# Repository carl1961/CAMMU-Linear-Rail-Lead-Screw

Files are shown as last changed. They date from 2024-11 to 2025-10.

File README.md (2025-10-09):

# CAMMU with Linear Rail Lead Screw and front mounted customized CAMUU Gates

[CAMMU Facebook](https://www.facebook.com/groups/996841964765478)

CAMMU-Linear-Rail-Lead-Screw

First Thanks  to  camnefdt/CAMMU https://github.com/camnefdt/CAMMU   for his work and allowing us to have fun.

Step and Stl files in Linear Rail, feel free to improve.

Front Selector 250mm Linear rail MGN9 9mm MGN9C block
Top back Selector  300mm Linear MGN9 9mm MGN9C block
Lead Screw 270mm 

# Progress

Filamentalist_V3_CAMMU_Enclosue v19

[CAMMU-Linear-Rail-Lead-Screw Test](https://www.facebook.com/share/v/1BHCnjoqrM/)

Drill Bit Handles for hand drilling parts
Drill Bit Handle v2

Needed to add PC4-M6 fitting for the Filamentalist Spool winder to work.




WIN_20250928_00_52_30_Pro

WIN_20250930_00_51_32_Pro

New Gate needs Slide nuts with these 12mm dummy slider spacers to keep nuts within range to bolt gates.

WIN_20250929_01_24_08_Pro

Made some changes to the original Gate, added bearings on the henges and made mounting in front , makes it easer to remove if need to be repaired. made some other minor changes too.

WIN_20250929_23_52_04_Pro  WIN_20250930_00_02_21_Pro

WIN_20250930_00_03_26_Pro  



You must use slider nuts instead of the hamer head nuts, so you will be able to hook the top. This also gave mor support for when the selector presses down to clamp filament.

lead screw came off a old anycubic I3  P, 





# CAMMU - V1

CAMMU is a universal multi material filament system, inspired by ERCF and Tradrack systems but designed to use no servo at all and keep components as accessible as possible.

A full custome controller and DIY controller is currently in the works and to be released soon. 2 stepper ports and 6 endstop connections are all that is needed if you build the 4 gate version.

Please feel free to contribute towards future projects and developments

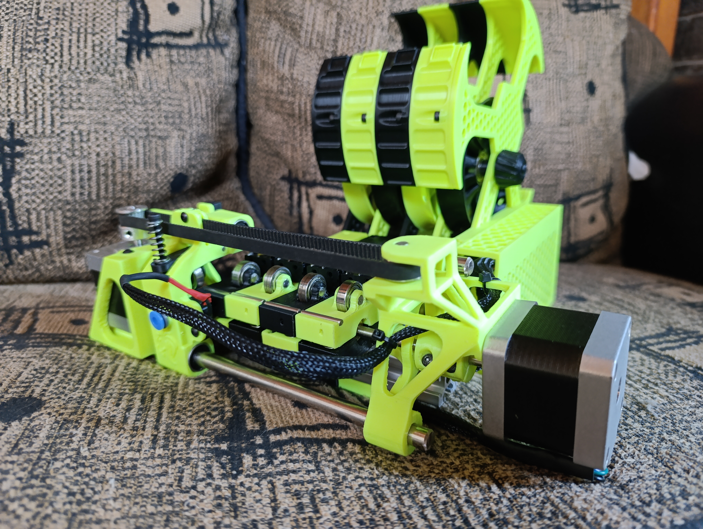
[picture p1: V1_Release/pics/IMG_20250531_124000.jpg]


[image]: https://github.com/camnefdt/CAMMU/blob/main/V1_Release/pics/IMG_20250531_124000.jpg
### Updates
- 06-08-2025:
    - Added CAMMU Gate Spacer to make the gate spacing a lot simpler
- 06-06-2025:
    - CAMMU Full release V1
    - Fixed folder structure and renamed old Beta to "CAMMU_Old"
    - Added modified ERCT-Cotton tail buffer files
    - **NOTE** The Cotton tail end cap with electronics was modified to fit BTT mmb V2 which is different size and mounting hole to MMB v1.
- 05-06-2025:
  - Added strengthened drive ends
  - Added slightly adjusted tension arm to align better on gate.
  - Added completed project photo.
- 01-04-2025:
  - Added modified top gate with thickened rear section for limit switch mount and enlarged screw holes for m3 screws.
- 12-03-2025:
  - Added build manual V1.
- 19-01-2025:
  - Added modified selector body to prevent premature wear of housing body.
  - Added slots to limit switch mounting on selector body.
  - Added strengthened selector drive end to limit unnecesary flex.
  - Moved extrude drive end idler pulley inward to make system more compact
  - Added more material on the bottom gate pivot ears to strengthen.
  - Modified to match new bottom gate ears as well as slotted limit switch mounting holes.
- 08-12-2024:
  - Added Build FAQ 
- 05-12-2024:
  - Add in basic instructions for assembly

### Build FAQ
- For the buffer, the ERCT (Cotton tail) buffer is a perfect fit. [***HERE***](https://github.com/Enraged-Rabbit-Community/ERCF_v2/tree/master/Recommended_Options/ERCT_Buffer)
- For the software control aspect of CAMMU, we decided to not reinvent the wheel and make use of the fantastic existing software called **Happy Hare** by moggieuk. You can find his github page [***HERE***](https://github.com/moggieuk)
  - You are requied to [***install Happy Hare***](https://github.com/moggieuk/Happy-Hare/wiki/Installation) on your existing klipper installation.
  - In due time we will compile a short guide on the installation and configuration of **Happy Hare**
- For the sensing aspect, not only do you require a filament sensor per gate, but also require a filament sensor on your toolhead
  - If you currently use the Sherpa range:
    - You can find a fantastic toolhead sensor for [***Sherpa Mini***](https://github.com/v6cl/MyDIYthings/tree/main/3Dprinters/AnnexEngineeringMOD/SherpaMini/SherpaMiniFilamentSensor).
      - This is a fantastic toolhead sensor and can easily be wired up to your existing toolhead board if you have one.
  - You also require a filament cutter on your toolhead as
    - The one we recommend and have tested can be found on Prusa Printables [***HERE***](https://www.printables.com/model/622289-filament-cutter-for-sherpa-and-sherpa-patterned-ex/files)

buy me a coffee
[***HERE***](https://www.buymeacoffee.com/camnefdt)


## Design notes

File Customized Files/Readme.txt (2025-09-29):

Gate bottom (NEW) takes 2 MR63zz bearings 3x6x2.5  , some list it as 3x6x3
Require to use 2020 M5 slide nuts
12mm Slider Nut dummy spacers, used to space Slider nuts the 22mm spacing

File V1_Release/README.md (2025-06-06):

V1 of CAMMU
Custom designed multi material system using no servo whatsoever

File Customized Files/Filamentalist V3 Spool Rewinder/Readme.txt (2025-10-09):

ALL still a work in progress!

My parts used in my 8 color Filamentalist Frame I did with 2020 extrusion
I resized clearance on parts at points to make easeir to assymble, for example the 8mm shaft I did 8.25mm  etc...  Filamentalist has everything exact measurements.

Also (optional) included or 3 drill handles I designed to make hand drilling, for the pockets for the earas to fit, I used M3 inserts for using 3mm allen screws to tighten the drill bit in handle.

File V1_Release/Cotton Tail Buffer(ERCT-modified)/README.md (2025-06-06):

Cotton tail buffer as found at: [***HERE***](https://github.com/Enraged-Rabbit-Community/ERCF_v2/tree/master/Recommended_Options/ERCT_Buffer)

Modified to suite CAMMU. 
This is the recommended option which fits perfect with CAMMU system

The electronic box was modified to fit BTT mmb V2 which is a different size and has different mounting holes copmpared to V1.

The bunny logo was also removed to make for easier printing.

The filament sensor space on filament blocks were removed as they are not necessary on CAMMU.

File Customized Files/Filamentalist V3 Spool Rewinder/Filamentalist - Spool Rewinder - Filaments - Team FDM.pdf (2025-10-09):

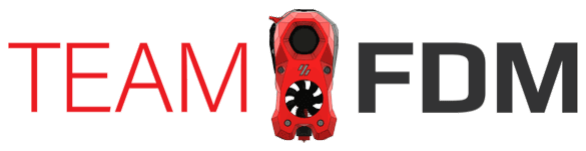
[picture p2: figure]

Filaments (https://www.teamfdm.com/forums/forum/38-filaments/)
- (https://www.teamfdm.com/discover/)
- (https://www.teamfdm.com/search/)

Home (https://www.teamfdm.com/) | Forums (https://www.teamfdm.com/forums/) | TeamFDM (https://www.teamfdm.com/forums/forum/17-teamfdm/) | Filaments (https://www.teamfdm.com/forums/forum/38-filaments/) | All Activity (https://www.teamfdm.com/discover/)

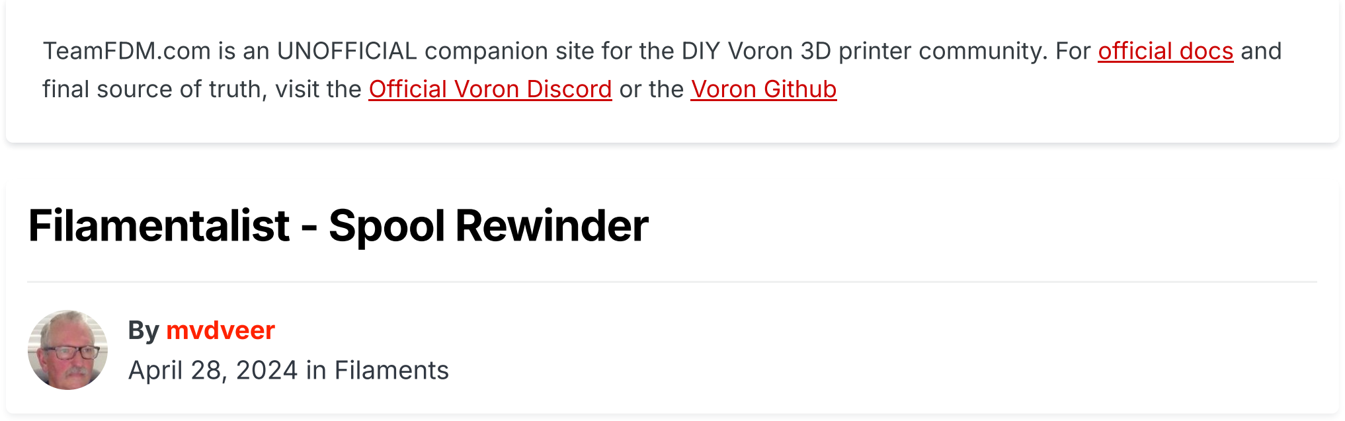
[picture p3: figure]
Filamentalist - Spool Rewinder; By mvdveer April 28, 2024 in Filaments

Reply to this topic

- (https://www.teamfdm.com/) | (https://www.teamfdm.com/forums/) | (https://www.teamfdm.com/forums/forum/17-teamfdm/) | (https://www.teamfdm.com/forums/forum/38-filaments/)

Filamentalist - Spool Rewinder
- (https://www.teamfdm.com/discover/)

TeamFDM.com is an UNOFFICIAL companion site for the DIY Voron 3D printer community. For official docs (https://bit.ly/VoronDocs) and final source of truth, visit the Official Voron Discord (https://bit.ly/VoronDiscord) or the Voron Github (https://bit.ly/VoronGitHub)

### mvdveer (https://www.teamfdm.com/profile/1268-mvdveer/)

Posted (https://www.teamfdm.com/forums/topic/3582-filamentalist-spool-rewinder/?do=findComment&comment=20390) April 28,
2024 (https://www.teamfdm.com/forums/topic/3582-filamentalist-spool-rewinder/?do=findComment&comment=20390)
- (https://www.teamfdm.com/profile/1268-mvdveer/)

Been looking for a good spool rewinder to use with the tradrack mounted on the Trident. Thanks to @PFarm (https://www.teamfdm.com/profile/5848-pfarm/) , I took a liking to the Filamentalist Spool Rewinder. (https://github.com/SkiBikePrint/ERCF_Mods/tree/main/Filamentalist) Tried quite a few and was not really happy with the solution I mounted on the Trident (Stern Wheeler Filament buffer). (https://www.printables.com/model/615902-stern-wheeler-filament-buffer-customizeable) Though it did not take up much space, it did not offer a flawless experience.

I also thought of the Universal Auto Rewind spool holder (https://www.printables.com/model/168-universal-auto-rewind-spool-holder-mm) by Vincent Groenhuis, as posted by @Buurman (https://www.teamfdm.com/profile/2667-buurman/) , but had an awful lot of trouble printing the springs to my satisfaction. Gave up on that one (heaps of parts in a tub, minus the springs).

So, filamentalsit seemed like a good idea, especially after watching the device in action:

https://www.youtube.com/watch?v=4iaSJrHc7k4

https://www.youtube.com/watch?v=W6pqgNZXvYI

Instructions on the GitHub page are comprehensive but I still found it confusing at times, and some steps that seemed obvious were omitted, like putting the rubber bands on the large pulleys.

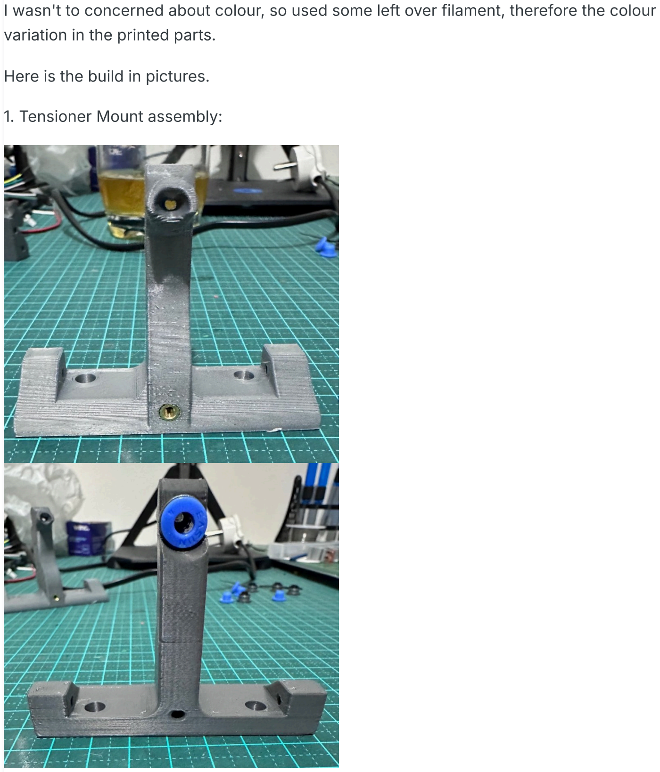
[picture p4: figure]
variation in the printed parts.; Here is the build in pictures.; 1. Tensioner Mount assembly:

I wasn't to concerned about colour, so used some left over filament, therefore the colour

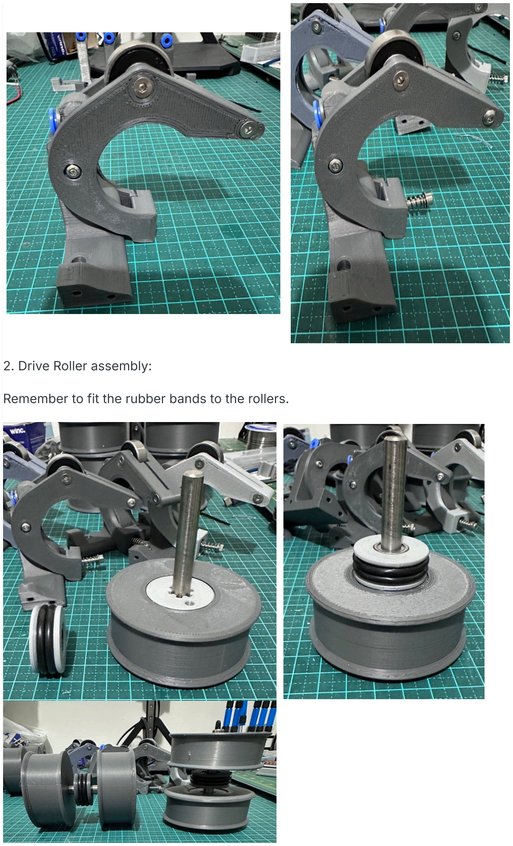
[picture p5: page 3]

2. Drive Roller assembly:

Remember to fit the rubber bands to the rollers.

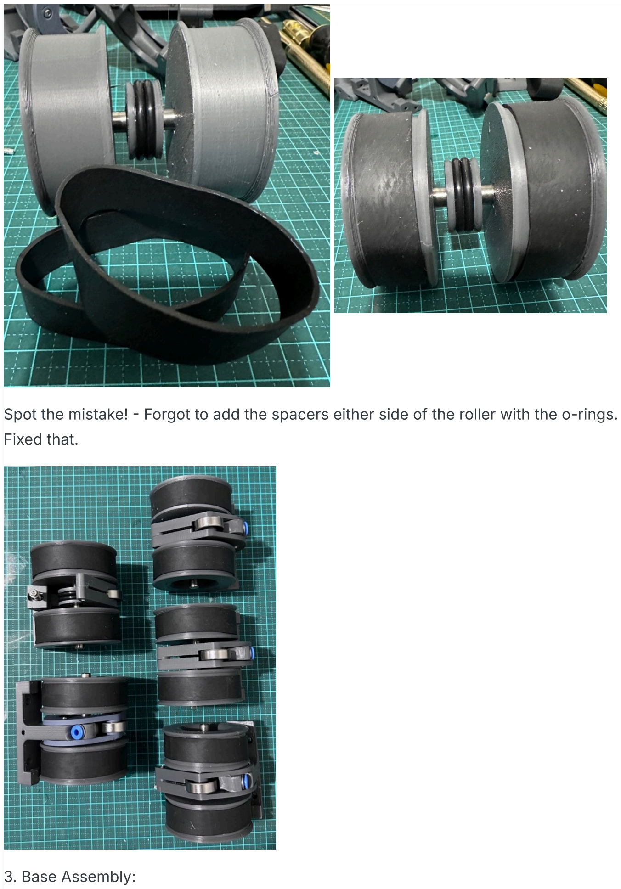
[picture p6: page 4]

Spot the mistake! - Forgot to add the spacers either side of the roller with the o-rings. Fixed that.

3. Base Assembly:

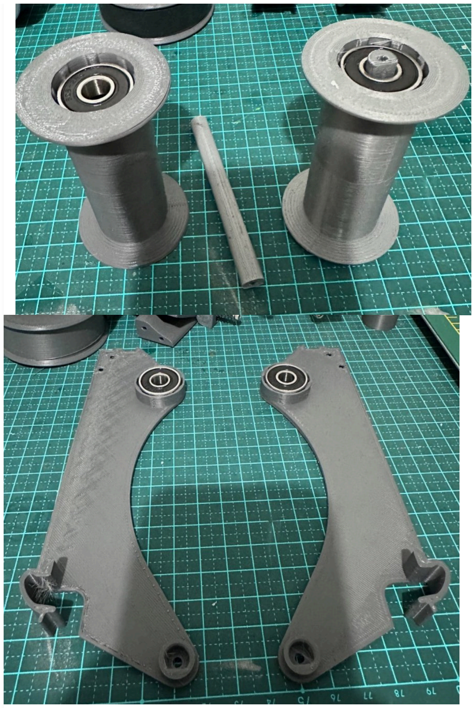
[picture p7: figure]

(Too much squish on the left pillar - see the wavey pattern)

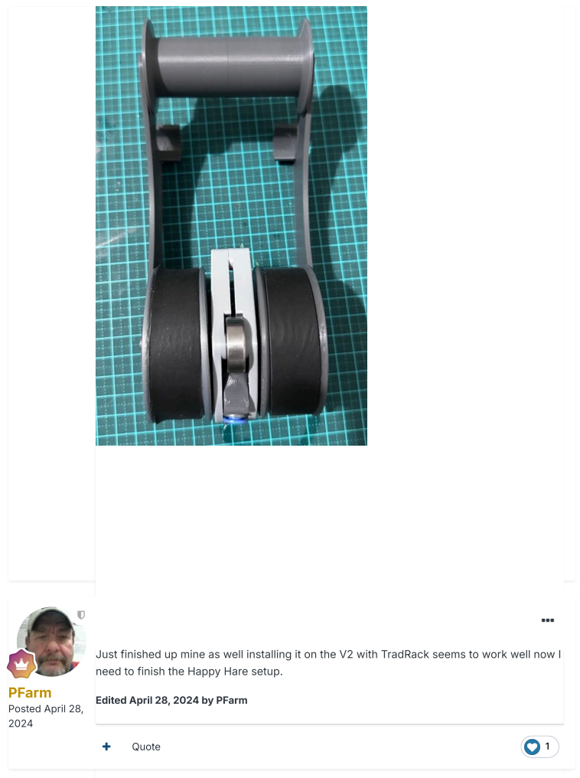
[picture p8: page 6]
PFarm; Posted April 28, 2024; Quote

Just finished up mine as well installing it on the V2 with TradRack seems to work well now I
need to finish the Happy Hare setup.

Edited April 28, 2024 by PFarm

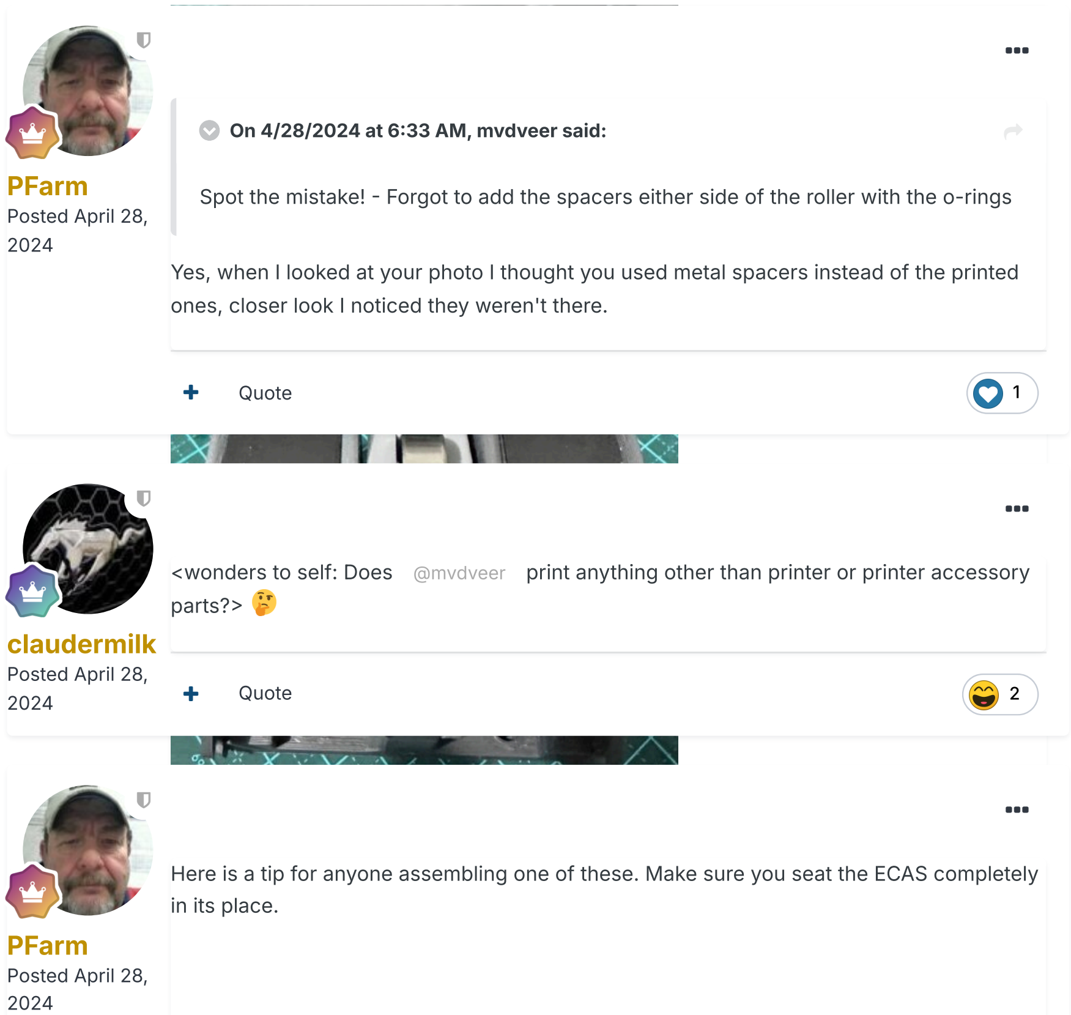
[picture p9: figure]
4. Finished Product:; PFarm; Posted April 28, 2024; Quote; On 4/28/2024 at 6:33 AM, mvdveer said:; claudermilk; parts?>; in its place.

Yes, when I looked at your photo I thought you used (https://www.teamfdm.com/uploads/monthly_2024_04/IMG_6572.jpeg.874148286c1fcb7fde601b39d7dd90a9.jpeg) metal spacers instead of the printed ones, closer look I noticed they weren't there.

Spot the mistake! - Forgot to add the spacers either (https://www.teamfdm.com/uploads/monthly_2024_04/IMG_6572.jpeg.874148286c1fcb7fde601b39d7dd90a9.jpeg) side of the roller with the o-rings

<wonders to self: Does @mvdveer print anything other (https://www.teamfdm.com/uploads/monthly_2024_04/IMG_6572.jpeg.874148286c1fcb7fde601b39d7dd90a9.jpeg) than printer or printer accessory

Here is a tip for anyone assembling one of these. Make sure you seat the ECAS completely

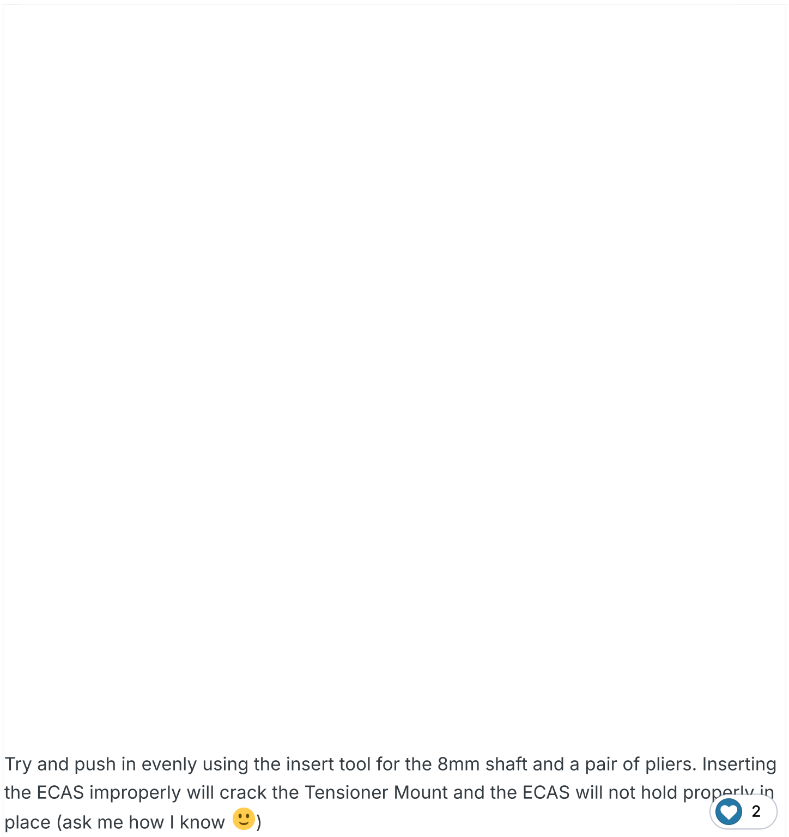
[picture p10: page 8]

And... it works! Even with these new cardboard spools - I do not like cardboard spools (https://www.teamfdm.com/uploads/monthly_2024_04/IMG_2212.JPG.8d0371010d1b7c2a49142156d88ff5b7.JPG) -just saying.

These will be installed on 2020 extrusion, mounted on top of the Trident. Thus, it will (https://www.teamfdm.com/uploads/monthly_2024_04/IMG_2212.JPG.8d0371010d1b7c2a49142156d88ff5b7.JPG) hide the tradrack at the back (https://www.teamfdm.com/uploads/monthly_2024_04/IMG_2212.JPG.8d0371010d1b7c2a49142156d88ff5b7.JPG)

Another enjoyable and easy build.

- Quote

Try and push in evenly using the insert tool for the 8mm shaft and a pair of pliers. Inserting the ECAS improperly will crack the Tensioner Mount and the ECAS will not hold properly in place (ask me how I know )

2

Got them installed on the 2020

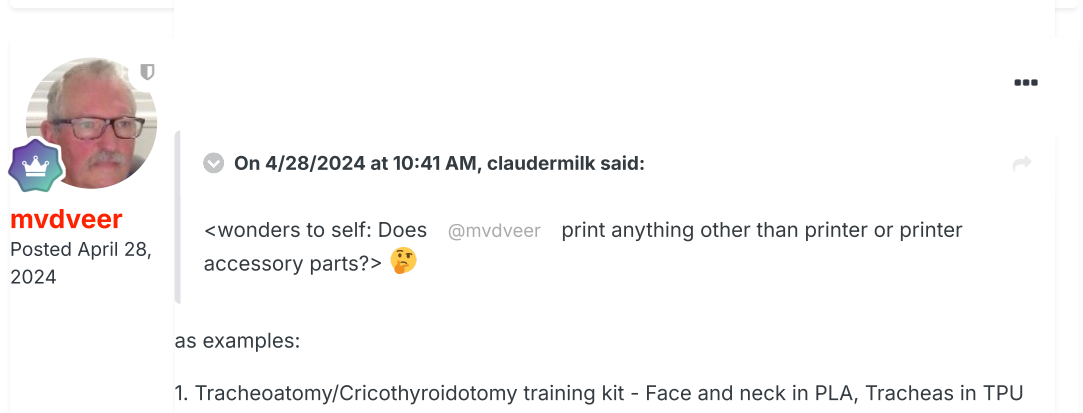
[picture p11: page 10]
mvdveer; Posted April 28, 2024; as examples:

On 4/28/2024 at 10:41 AM, claudermilk said:

<wonders to self: Does @mvdveer print anything other than printer or printer
accessory parts?>

1. Tracheoatomy/Cricothyroidotomy training kit - Face and neck in PLA, Tracheas in TPU

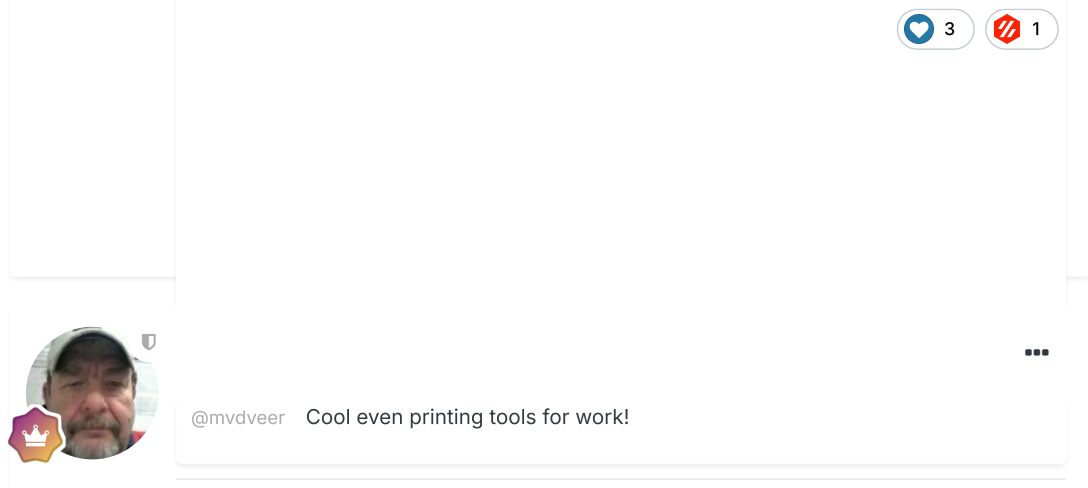
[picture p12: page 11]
Quote

Edited April 29, 2024 by PFarm

(https://www.teamfdm.com/profile/5848-pfarm/)

@mvdveer Cool even printing tools for work! (https://www.teamfdm.com/uploads/monthly_2024_04/IMG_5512.png.775a7b3a7bd59620c0779ff4b69a714a.png)

2. Marcus Aerilius Bust - PLA Marble - pre "post printing processing:
- Quote

### PFarm (https://www.teamfdm.com/profile/5848-pfarm/)

Posted (https://www.teamfdm.com/forums/topic/3582-filamentalist-spool-rewinder/?do=findComment&comment=20411) April 28,
2024 (https://www.teamfdm.com/forums/topic/3582-filamentalist-spool-rewinder/?do=findComment&comment=20411)
- Quote

### Graymattor (https://www.teamfdm.com/profile/10383-graymattor/)

Posted (https://www.teamfdm.com/forums/topic/3582-filamentalist-spool-rewinder/?do=findComment&comment=20423) April 29,
2024 (https://www.teamfdm.com/forums/topic/3582-filamentalist-spool-rewinder/?do=findComment&comment=20423)

# G (https://www.teamfdm.com/profile/10383-graymattor/)

Thanks for sharing your experiences,

I have been looking at the Filamentalis (https://www.teamfdm.com/uploads/monthly_2024_04/IMG_6302.png.69055e738b2675f11c40c1fc338679d3.png)t for a while now, due to space constraints (https://www.teamfdm.com/uploads/monthly_2024_04/IMG_6303.png.29f3bddd6825d8a3c81160afd4d6465b.png) a buffer was going to be difficult, and this woul (https://www.teamfdm.com/uploads/monthly_2024_04/IMG_6302.png.69055e738b2675f11c40c1fc338679d3.png)d be perfect for my 'future' set up! there (https://www.teamfdm.com/uploads/monthly_2024_04/IMG_6303.png.29f3bddd6825d8a3c81160afd4d6465b.png) appears to be quire a few people know who have (https://www.teamfdm.com/uploads/monthly_2024_04/IMG_6302.png.69055e738b2675f11c40c1fc338679d3.png) had some great success with it, i need (https://www.teamfdm.com/uploads/monthly_2024_04/IMG_6303.png.29f3bddd6825d8a3c81160afd4d6465b.png) to order some parts for a printer build so i will (https://www.teamfdm.com/uploads/monthly_2024_04/IMG_6302.png.69055e738b2675f11c40c1fc338679d3.png) order the Filamentalist parts also (shame (https://www.teamfdm.com/uploads/monthly_2024_04/IMG_6303.png.29f3bddd6825d8a3c81160afd4d6465b.png) no AliExpress links, being in the UK i cann (https://www.teamfdm.com/uploads/monthly_2024_04/IMG_6302.png.69055e738b2675f11c40c1fc338679d3.png)ot use the Amazon links, however a lot (https://www.teamfdm.com/uploads/monthly_2024_04/IMG_6303.png.29f3bddd6825d8a3c81160afd4d6465b.png) of items do come up on Amazon when copying the descriptions.

Please continue to share your experiences as you use it and of course set up with Happy Hare, which is something i am not looking forward to!!

Thanks

- Quote

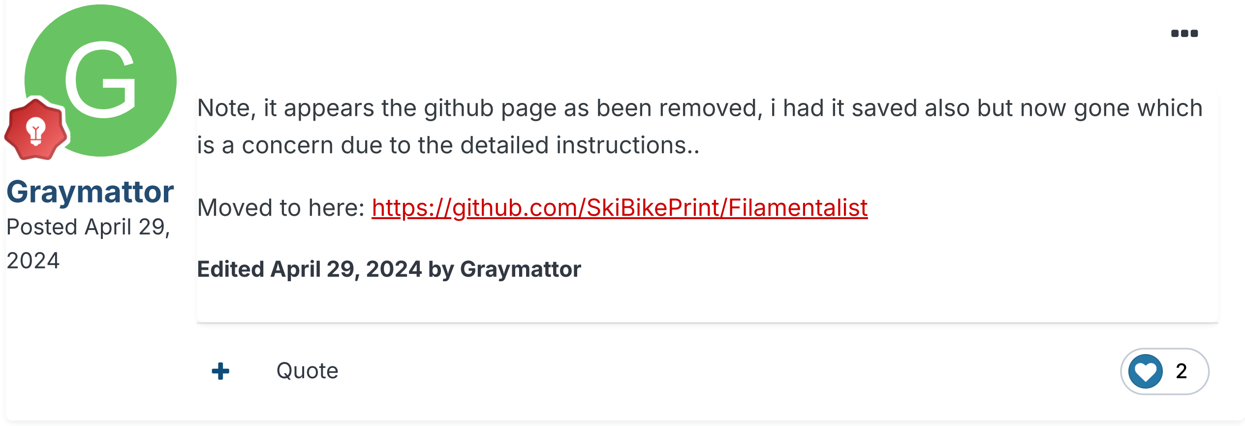
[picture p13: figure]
Graymattor; Posted April 29, 2024; Moved to here: https://github.com/SkiBikePrint/Filamentalist; Edited April 29, 2024 by Graymattor; Quote

Note, it appears the github page as been removed, i had it saved also but now gone which is a concern due to the detailed instructions..

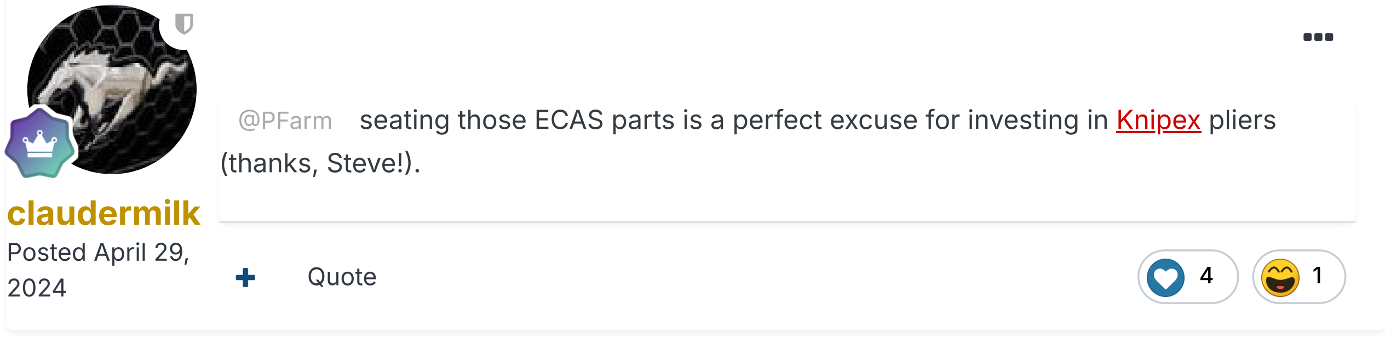
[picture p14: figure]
claudermilk; Posted April 29, 2024; (thanks, Steve!).; Quote

@PFarm (https://www.teamfdm.com/profile/5848-pfarm/) seating those ECAS parts is a perfect excuse for investing in Knipex (https://amzn.to/3IGSgyu) pliers

4

1

2

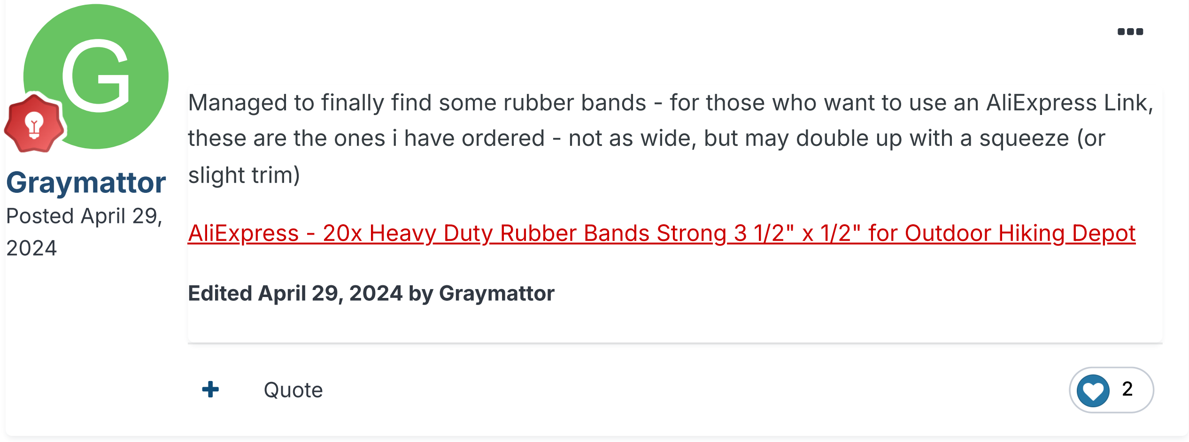
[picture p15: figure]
Graymattor; Posted April 29, 2024; slight trim); Edited April 29, 2024 by Graymattor; Quote

Managed to finally find some rubber bands - for those who want to use an AliExpress Link, these are the ones i have ordered - not as wide, but may double up with a squeeze (or

AliExpress - 20x Heavy Duty Rubber Bands Strong 3 1/2" x 1/2" for Outdoor Hiking Depot (https://www.aliexpress.com/item/1005006315999981.html?src=google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)

### PFarm (https://www.teamfdm.com/profile/5848-pfarm/)

Posted (https://www.teamfdm.com/forums/topic/3582-filamentalist-spool-rewinder/?do=findComment&comment=20439) April 29,
2024 (https://www.teamfdm.com/forums/topic/3582-filamentalist-spool-rewinder/?do=findComment&comment=20439)
- (https://www.teamfdm.com/profile/5848-pfarm/)

That should work mine were 3/4" wide as long as you push the rubber band toward the outside edge of the roller that's where the filament reel makes contact.

On 4/29/2024 at 9:51 AM, Graymattor (https://www.teamfdm.com/?app=core&module=members&controller=profile&id=10383) said:

Managed to finally find some rubber bands - for those who want to use an AliExpress Link, these are the ones i have ordered - not as wide, but may double up with a squeeze (or slight trim)

AliExpress - 20x Heavy Duty Rubber Bands Strong 3 1/2" x 1/2" for Outdoor Hiking Depot (https://www.aliexpress.com/item/1005006315999981.html?src=google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)

- (https://www.teamfdm.com/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)

- Quote

### Graymattor (https://www.teamfdm.com/profile/10383-graymattor/)

Posted (https://www.teamfdm.com/forums/topic/3582-filamentalist-spool-rewinder/?do=findComment&comment=20444) April 29,
2024 (https://www.teamfdm.com/forums/topic/3582-filamentalist-spool-rewinder/?do=findComment&comment=20444)

# G (https://www.teamfdm.com/profile/10383-graymattor/)

Thanks or the info, i just could not find 3/4" wide bands any where!

All the parts i don't already have in a stash somewhere have been ordered, next to go on a printing marathon! i will be looking at setting up 12 of these! i think may be in a row of 7 and then 5 in front staggered to allow the PTFE through from the rear ones..

I have absolutely no idea what im doing, but down the hole i goooooo!!

At least i now know i don't need to build up the ERCT

Edited April 30, 2024 by Graymattor (https://www.teamfdm.com/uploads/monthly_2024_04/IMG_6569_Fotor.jpg.2aeb5aa6f53a69e8d7b8f7f7add18166.jpg)

- Quote

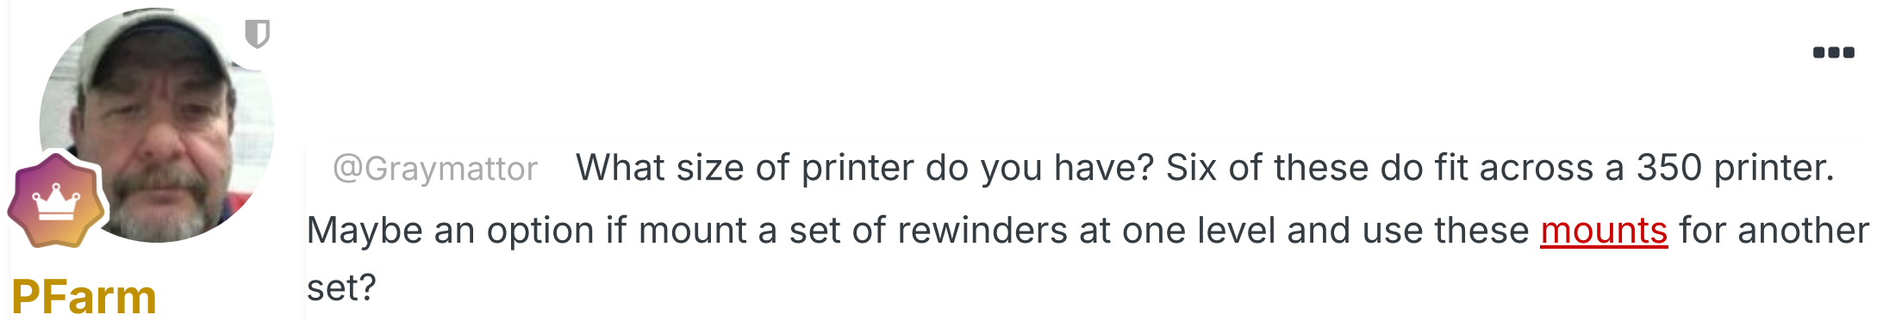
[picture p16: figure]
PFarm; set?

@Graymattor (https://www.teamfdm.com/profile/10383-graymattor/) What size of printer do you have? Six of these do fit across a 350 printer. Maybe an option if mount a set of rewinders at one level and use these mounts (https://www.printables.com/model/530709-offset-2020-mount-for-vorons) for another

21

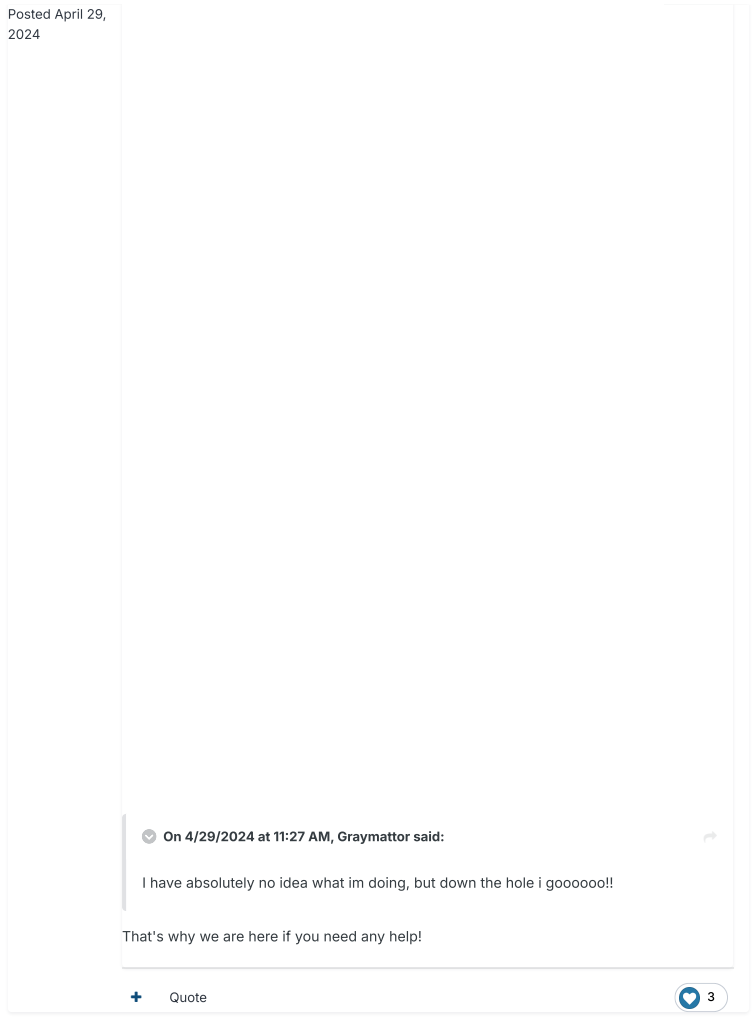
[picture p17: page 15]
Posted April 29, 2024; Quote

On 4/29/2024 at 11:27 AM, Graymattor (https://www.teamfdm.com/?app=core&module=members&controller=profile&id=10383) said:

I have absolutely no idea what im doing, but down the hole i goooooo!!

That's why we are here if you need any help!

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
### r (https://www.teamfdm.com/profile/10383-graymattor/)

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
ril 3

0

,
2

0

2

4 (https://www.teamfdm.com/forums/topic/3582-filamentalist-spool-rewinder/?do=findComment&comment=20480)

# G (https://www.teamfdm.com/profile/10383-graymattor/)

1 month later...

4 weeks later... (https://www.teamfdm.com/uploads/monthly_2024_04/e8276fa7-cbd9-46fb-b81e-03d47c97bf0e.jpg.f02f6d9da4d301cebe93664a2baefc46.jpg)

It's actually going in the top of a purpose built enclosure which is 600mm wide x 800mm deep... but need to fit 12 spools and the ERCF in there and allow enough room for the reverse bowden in to the printer compartment below...

Thank you.... When I start wiring, happy hare and integration that's when I'll hit a wall! I'll be using the MMB but currently I don't have a CAN printer (I have a klipperised CR-10

150 (https://www.teamfdm.com/profile/12812-wackocrash5150/) Posted (https://www.teamfdm.com/forums/topic/3582-filamentalist-spool-rewinder/?do=findComment&comment=22375) June 24, 2024 (https://www.teamfdm.com/forums/topic/3582-filamentalist-spool-rewinder/?do=findComment&comment=22375) | smart pro and I'm most of the way through building VZ330, i need to get both running CAN)..
- Quote

Wackocrash (https://www.teamfdm.com/profile/12812-wackocrash5150/)5 (https://www.teamfdm.com/uploads/monthly_2024_04/e8276fa7-cbd9-46fb-b81e-03d47c97bf0e.jpg.f02f6d9da4d301cebe93664a2baefc46.jpg)

Hello there. I just wanted to ask if you're still using (https://www.teamfdm.com/uploads/monthly_2024_04/e8276fa7-cbd9-46fb-b81e-03d47c97bf0e.jpg.f02f6d9da4d301cebe93664a2baefc46.jpg) these and if you're happy with them thus far? Any hiccups you've noticed? I too am looking (https://www.teamfdm.com/uploads/monthly_2024_04/e8276fa7-cbd9-46fb-b81e-03d47c97bf0e.jpg.f02f6d9da4d301cebe93664a2baefc46.jpg) to build a few of these for a Tradrack. Just ordered the BOM parts from Amazon. (https://www.teamfdm.com/uploads/monthly_2024_04/e8276fa7-cbd9-46fb-b81e-03d47c97bf0e.jpg.f02f6d9da4d301cebe93664a2baefc46.jpg) Thanks in advance.

- Quote (https://www.teamfdm.com/uploads/monthly_2024_04/e8276fa7-cbd9-46fb-b81e-03d47c97bf0e.jpg.f02f6d9da4d301cebe93664a2baefc46.jpg)

### mvdveer (https://www.teamfdm.com/profile/1268-mvdveer/)

Posted (https://www.teamfdm.com/forums/topic/3582-filamentalist-spool-rewinder/?do=findComment&comment=22379) June 24,
2024 (https://www.teamfdm.com/forums/topic/3582-filamentalist-spool-rewinder/?do=findComment&comment=22379)
- (https://www.teamfdm.com/profile/1268-mvdveer/)

Yes - they have been working without an issue

- Quote

On 6/24/2024 at 9:01 AM, Wackocrash5150 said:

Hello there. I just wanted to ask if you're still using (https://www.teamfdm.com/uploads/monthly_2024_04/e8276fa7-cbd9-46fb-b81e-03d47c97bf0e.jpg.f02f6d9da4d301cebe93664a2baefc46.jpg) these and if you're happy with them thus far? Any hiccups you've noticed? I too (https://www.teamfdm.com/uploads/monthly_2024_04/e8276fa7-cbd9-46fb-b81e-03d47c97bf0e.jpg.f02f6d9da4d301cebe93664a2baefc46.jpg) am looking to build a few of these for a Tradrack. Just ordered the BOM parts from Amazon. (https://www.teamfdm.com/uploads/monthly_2024_04/e8276fa7-cbd9-46fb-b81e-03d47c97bf0e.jpg.f02f6d9da4d301cebe93664a2baefc46.jpg) Thanks in advance.

- (https://www.teamfdm.com/uploads/monthly_2024_04/e8276fa7-cbd9-46fb-b81e-03d47c97bf0e.jpg.f02f6d9da4d301cebe93664a2baefc46.jpg)
- (https://www.teamfdm.com/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)

### Guest

Posted (https://www.teamfdm.com/forums/topic/3582-filamentalist-spool-rewinder/?do=findComment&comment=22856) July 18,
2024 (https://www.teamfdm.com/forums/topic/3582-filamentalist-spool-rewinder/?do=findComment&comment=22856)

Edited December 22, 2024 by 5twenty (https://www.teamfdm.com/uploads/monthly_2024_04/e8276fa7-cbd9-46fb-b81e-03d47c97bf0e.jpg.f02f6d9da4d301cebe93664a2baefc46.jpg)

- | Quote | 2

2

### SkiBikeMak e (https://www.teamfdm.com/profile/6271-skibikemake/)

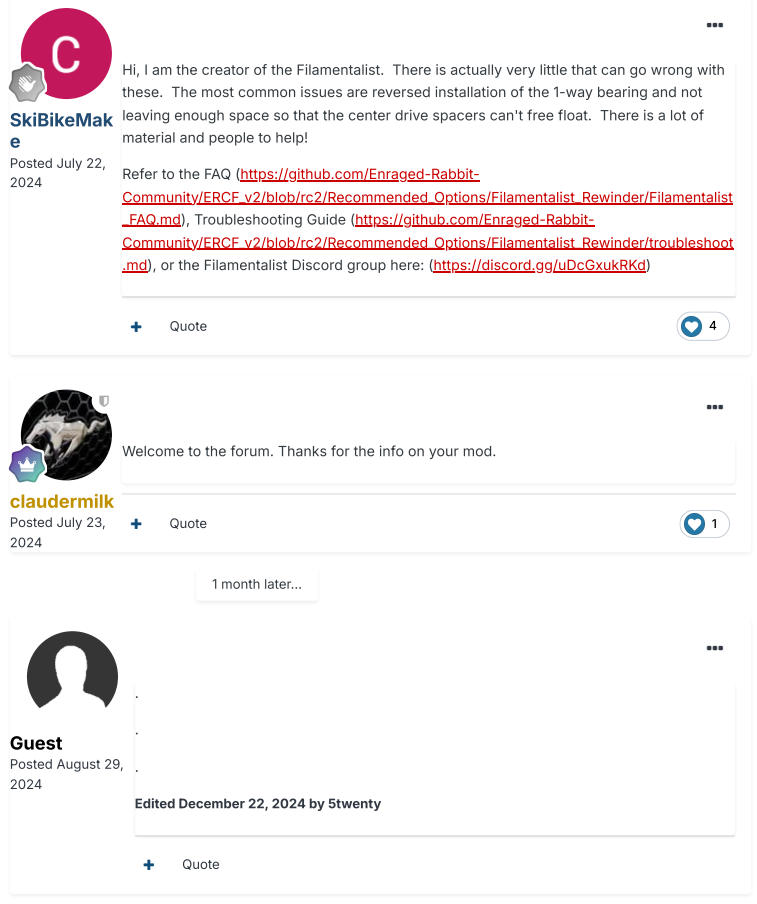
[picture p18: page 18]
1 month later...; Posted July 22, 2024; Quote; claudermilk; Posted July 23, 2024; Guest; Posted August 29, 2024

Hi, I am the creator of the Filamentalist. There is actually very little that can go wrong with
these. The most common issues are reversed installation of the 1-way bearing and not
leaving enough space so that the center drive spacers can't free float. There is a lot of
material and people to help!

Refer to the FAQ (https://github.com/Enraged-Rabbit-
Community/ERCF_v2/blob/rc2/Recommended_Options/Filamentalist_Rewinder/Filamentalist
_FAQ.md), (https://github.com/Enraged-Rabbit-Community/ERCF_v2/blob/rc2/Recommended_Options/Filamentalist_Rewinder/Filamentalist_FAQ.md) Troubleshooting Guide (https://github.com/Enraged-Rabbit-
Community/ERCF_v2/blob/rc2/Recommended_Options/Filamentalist_Rewinder/troubleshoot
.md), (https://github.com/Enraged-Rabbit-Community/ERCF_v2/blob/rc2/Recommended_Options/Filamentalist_Rewinder/troubleshoot.md) or the Filamentalist Discord group here: (https://discord.gg/uDcGxukRKd)

Welcome to the forum. Thanks for the info on your mod.

Edited December 22, 2024 by 5twenty

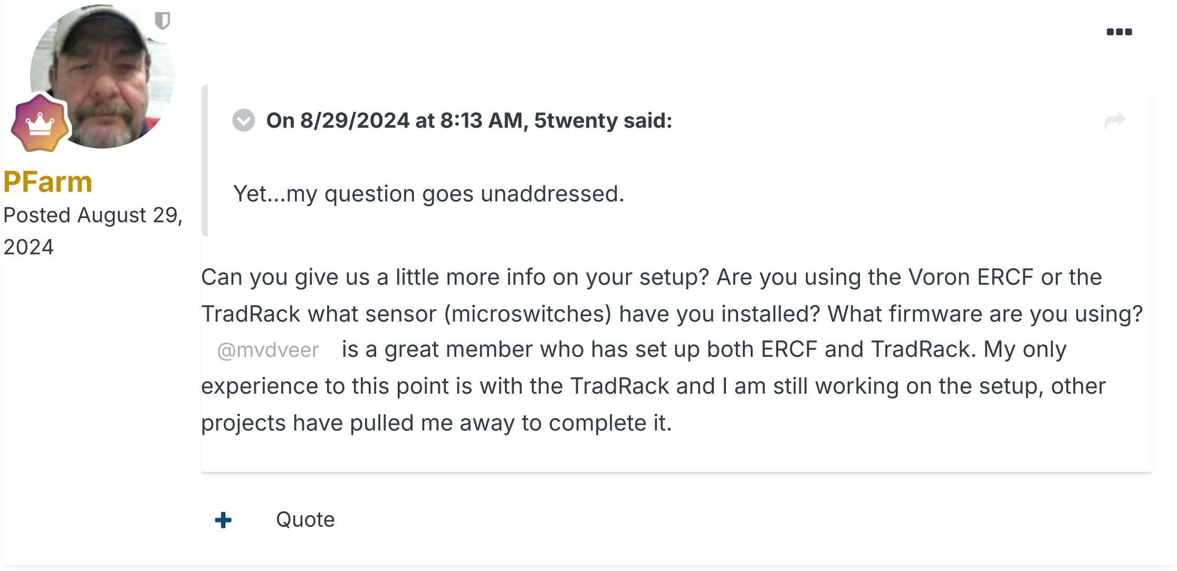
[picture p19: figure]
PFarm; Posted August 29, 2024; Quote; On 8/29/2024 at 8:13 AM, 5twenty said:; Yet...my question goes unaddressed.

Can you give us a little more info on your setup? Are you using the Voron ERCF or the TradRack what sensor (microswitches) have you installed? What firmware are you using? @mvdveer (https://www.teamfdm.com/profile/1268-mvdveer/) is a great member who has set up both ERCF and TradRack. My only experience to this point is with the TradRack and I am still working on the setup, other projects have pulled me away to complete it.

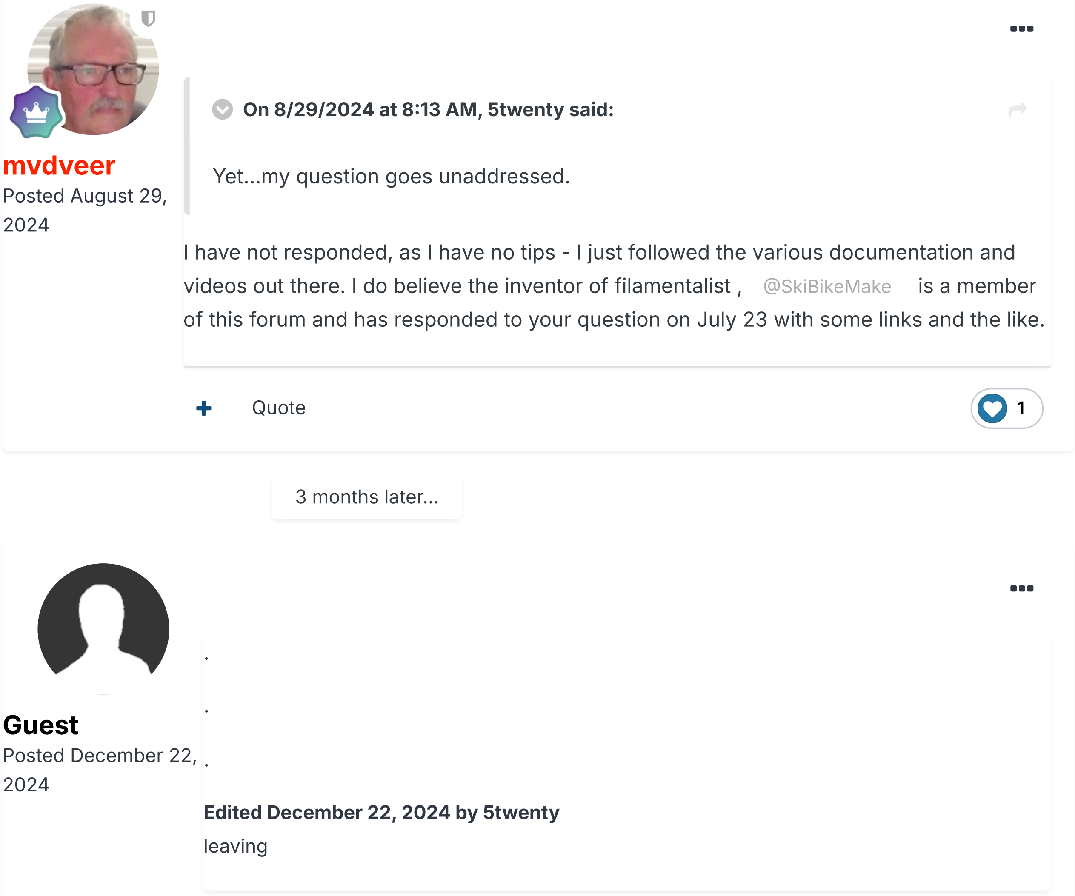
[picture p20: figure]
3 months later...; mvdveer; Posted August 29, 2024; Quote; On 8/29/2024 at 8:13 AM, 5twenty said:; Yet...my question goes unaddressed.; Guest; Posted December 22, 2024; Edited December 22, 2024 by 5twenty; leaving

I have not responded, as I have no tips - I just followed the various documentation and videos out there. I do believe the inventor of filamentalist , @SkiBikeMake (https://www.teamfdm.com/profile/6271-skibikemake/) is a member of this forum and has responded to your question on July 23 with some links and the like.

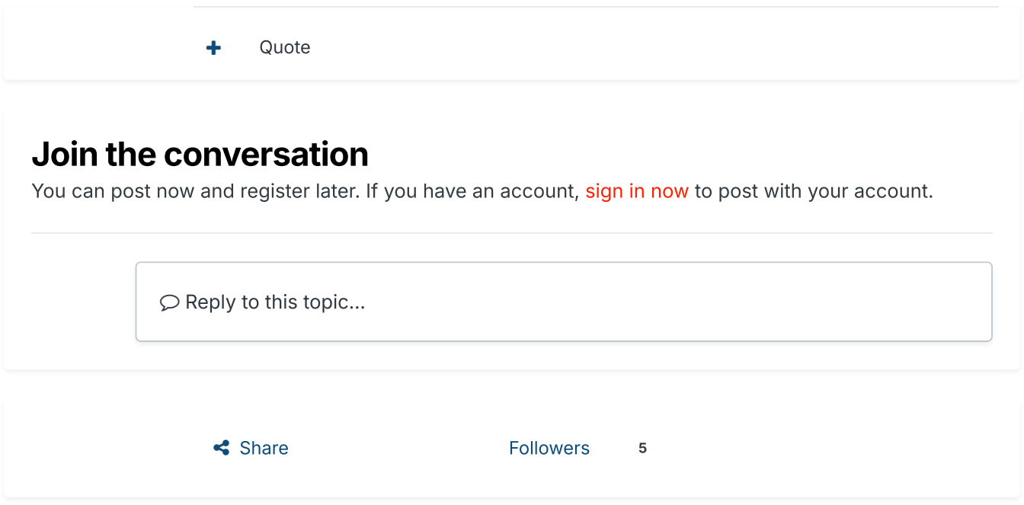
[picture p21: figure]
Join the conversation; Share; Followers; Quote; Reply to this topic...

You can post now and register later. If you have an account, sign in now (https://www.teamfdm.com/login/) to post with your account.

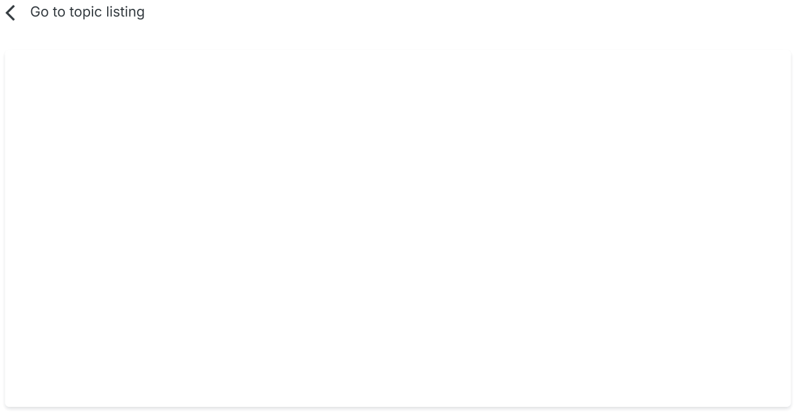
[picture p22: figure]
Go to topic listing

Home (https://www.teamfdm.com/) | Forums (https://www.teamfdm.com/forums/) | TeamFDM (https://www.teamfdm.com/forums/forum/17-teamfdm/) | Filaments (https://www.teamfdm.com/forums/forum/38-filaments/) | All Activity (https://www.teamfdm.com/discover/)
- (https://www.teamfdm.com/) | (https://www.teamfdm.com/forums/) | (https://www.teamfdm.com/forums/forum/17-teamfdm/) | (https://www.teamfdm.com/forums/forum/38-filaments/)

Filamentalist - Spool Rewinder
- (https://www.teamfdm.com/discover/)

Privacy Policy (https://www.teamfdm.com/privacy/) Contact Us (https://www.teamfdm.com/contact/) Community Guidelines (https://www.teamfdm.com/guidelines/)

Links on this site may earn a small commission at no cost to you. As an Amazon Associate the site earns from qualifying purchases. All monetized links go to support the site hosting and maintenance costs for all visitors.

- (https://www.facebook.com/teamfdm) | (https://twitter.com/teamfdm1) | (https://www.youtube.com/channel/UCNLAlS1upsdqGwGzgO3Ah7A)

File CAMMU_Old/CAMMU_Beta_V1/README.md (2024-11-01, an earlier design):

Beta V1 of CAMMU
Custom designed multi material system using no servo whatsoever

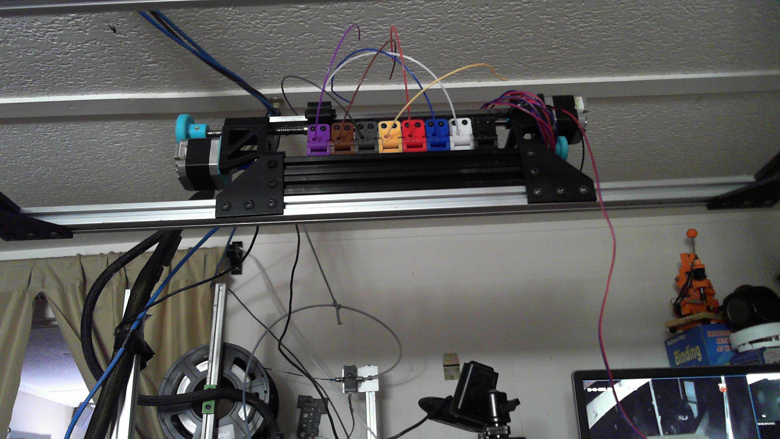
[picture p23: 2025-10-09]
Customized Files/Filamentalist V3 Spool Rewinder/WIN_20251005_20_56_37_Pro.jpg

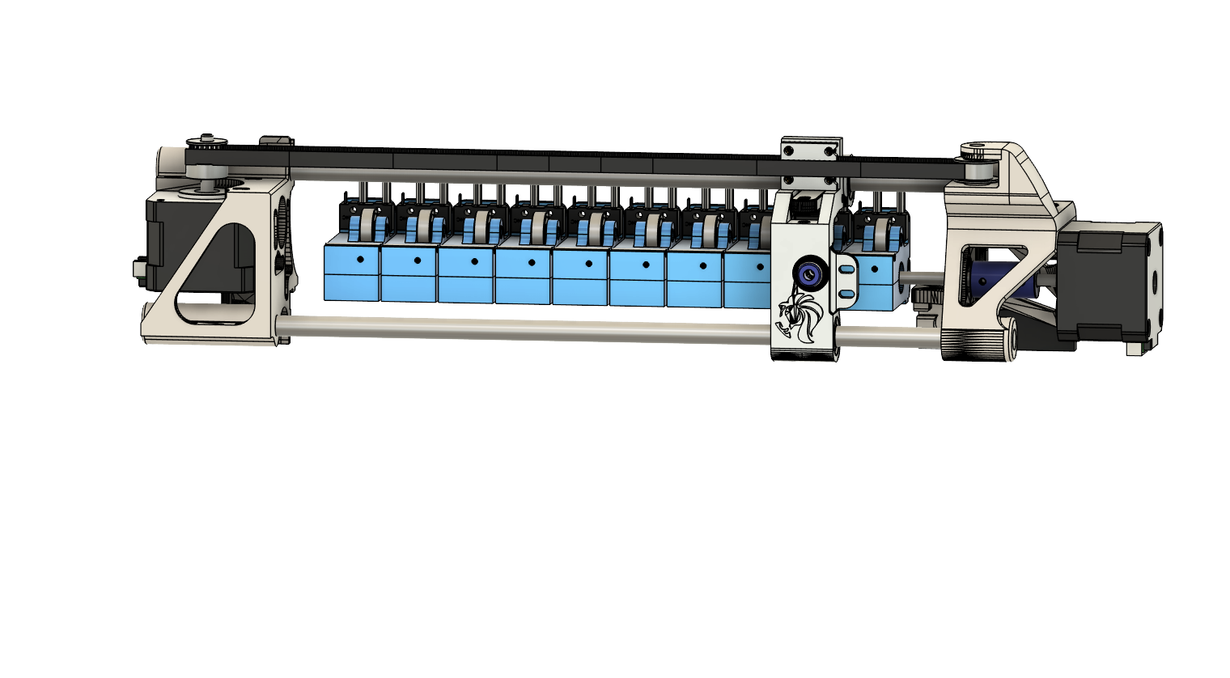
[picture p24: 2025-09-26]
Customized Files/Belt Driven/CAMMU v32.png

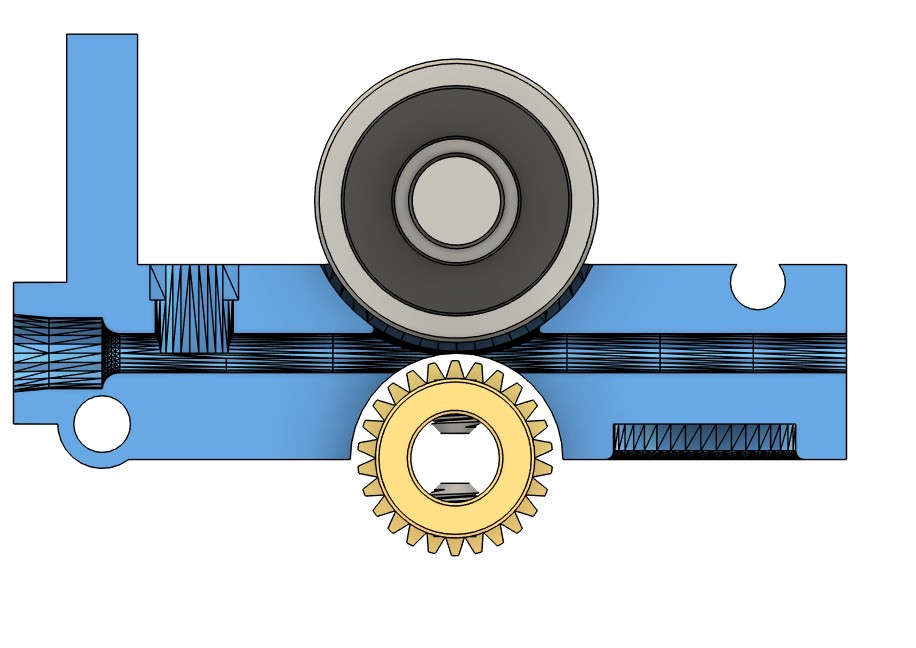
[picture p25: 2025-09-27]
Customized Files/original gate.jpg

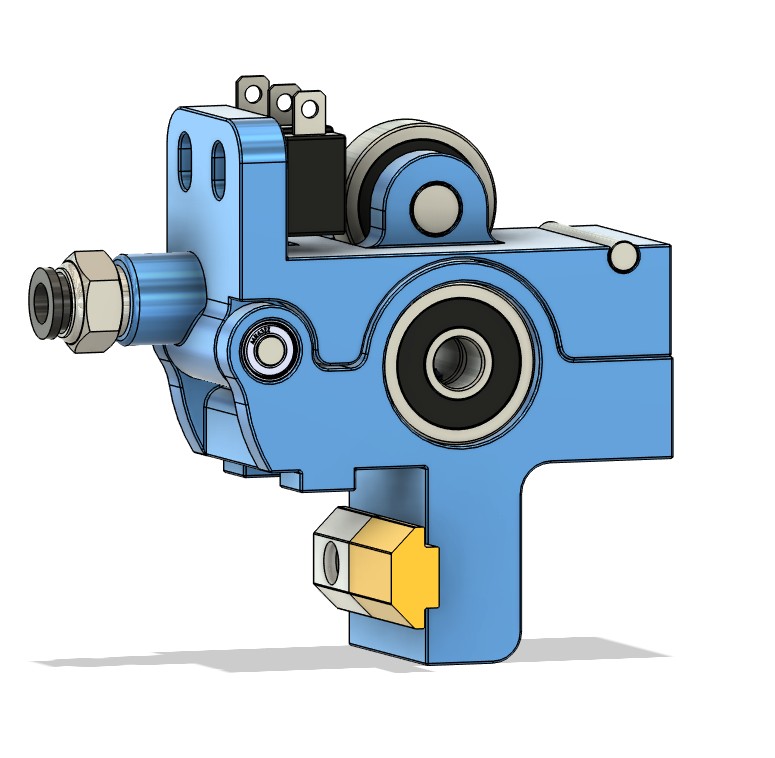
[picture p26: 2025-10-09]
Customized Files/Screenshot 2025-10-09 092926.jpg

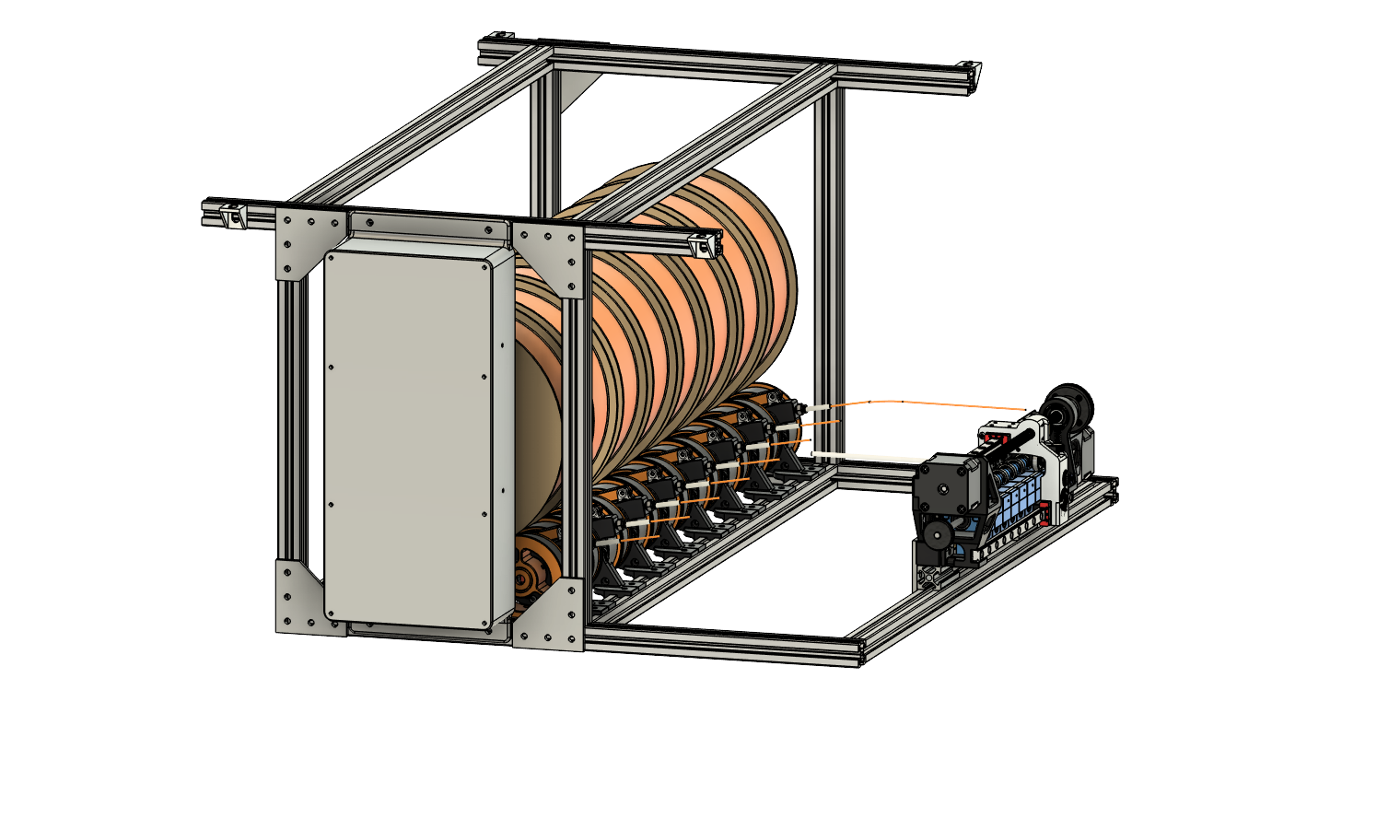
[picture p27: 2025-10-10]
Customized Files/Filamentalist V3 Spool Rewinder/CAD/Filamentalist_V3_CAMMU_Enclosue v22.png

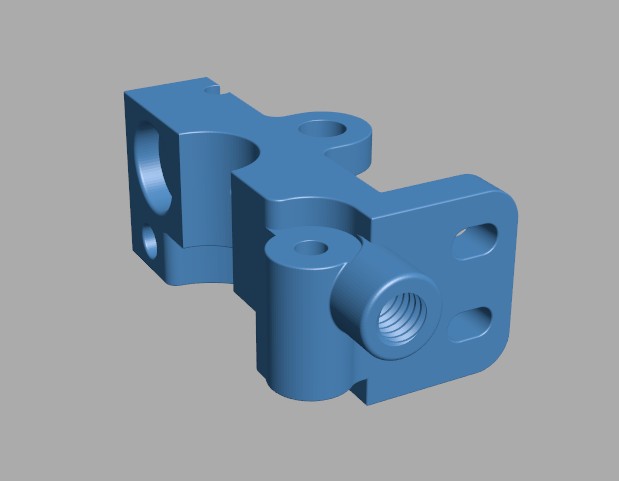
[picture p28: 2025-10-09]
Customized Files/Screenshot 2025-10-09 093540.jpg

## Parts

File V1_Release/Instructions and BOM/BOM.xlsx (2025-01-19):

CAMMU BOM
Category | Part | QTY | Comments | Link
Gate | 10x2 Magnet | 2 |  | https://magnetstore.co.za/products/10x2mm-n38-ni-neodymium-disc
 | 625 bearing | 2 |  | https://3dprintingstore.co.za/products/bearing-625-2rs
 | Extruder gear | 1 |  | https://3dprintingstore.co.za/products/extruder-gear-for-direct-drive-extruder-11mm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
 | 21x3mm shaft | 2 |  | https://www.netram.co.za/open-build/8945-smooth-round-bar-3mm.html
 | 12x5mm shaft | 1 |  | https://www.netram.co.za/open-build/8950-smooth-round-bar-5mm.html
 | limit switch | 1 |  | https://apexinvent.co.za/products/microswitch-20mm-x-9-5mm?_pos=4&_sid=566c43e40&_ss=r
 | M5x12 bolt | 1
 | M5 T-nut | 1 |  | https://apexinvent.co.za/products/t-nuts-for-20-series-extrusions?variant=41180604858483
 | M3x16 | 1
 | 4mm ball bearing | 1 |  | https://bearingsonlinesa.co.za/shop/s-balls-4mm-carbon-gd-1000/?gad_source=1
 | m3x10 | 2
Selector | LM8UU | 2 |  | https://www.communica.co.za/products/hkd-linear-ball-bearing-8mm?variant=31933933092937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
 | 8mm Shaft | 2 | Custom Length | https://3dprintingstore.co.za/products/linear-chromed-steel-rod-8mm-350mm?_pos=12&_sid=c951e9a9e&_ss=r
 | 21x3mm shaft | 1
 | 625 bearing | 1 |  | https://3dprintingstore.co.za/products/bearing-625-2rs
 | M5x10 bolt | 1
 | 16mm spring | 1
 | m3 heatsert | 1 |  | https://apexinvent.co.za/products/threaded-insert-m3x4mm-100-pcs-for-voron?_pos=1&_sid=eadaba180&_ss=r
 | m3x25 screw | 1
 | M3 washer | 1
 | M3x10 bolt | 1
 | M3 washer | 1
 | limit switch | 1 |  | https://apexinvent.co.za/products/microswitch-20mm-x-9-5mm?_pos=4&_sid=566c43e40&_ss=r
 | 4mm ball bearing | 2 |  | https://bearingsonlinesa.co.za/shop/s-balls-4mm-carbon-gd-1000/?gad_source=1
 | M3x10 bolt | 2
 | F695ZZ bearing | 2 |  | https://www.pishop.co.za/store/f695zz-5mmx13mmx4mm-double-shielded-flanged-ball-bearings
Motion | GT2 belt |  | Custom Length | https://www.netram.co.za/belts-gear/8892-6mm-gt2-open-ended-belt-1-meter.html
 | 20T 5mm bore | 1 |  | https://www.netram.co.za/belts-gear/8895-gt2-pulley-8mm-bore-20-teeth-6mm-belt.html
 | 625 bearing | 2 |  | https://3dprintingstore.co.za/products/bearing-625-2rs
 | NEMA17 | 2 |  | https://www.communica.co.za/products/hkd-stepper-motor-34mm-nema-17?variant=31916107792457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
 | limit switch | 1 |  | https://apexinvent.co.za/products/microswitch-20mm-x-9-5mm?_pos=4&_sid=566c43e40&_ss=r
 | m3x6 | 5
 | m3x10 | 4
 | m3 heatset | 2 | Coupler | https://apexinvent.co.za/products/threaded-insert-m3x4mm-100-pcs-for-voron?_pos=1&_sid=eadaba180&_ss=r
 | 3mm rod |  |  | https://www.netram.co.za/open-build/8945-smooth-round-bar-3mm.html
 | M5x12 | 3
 | M5 T-nut | 3 |  | https://apexinvent.co.za/products/t-nuts-for-20-series-extrusions?variant=41180604858483
 | 5x17mm rod | 1 |  | https://www.netram.co.za/open-build/8950-smooth-round-bar-5mm.html
MCU | STM32F401 | 1 |  | https://www.robotics.org.za/STM32F401CCU6-MOD

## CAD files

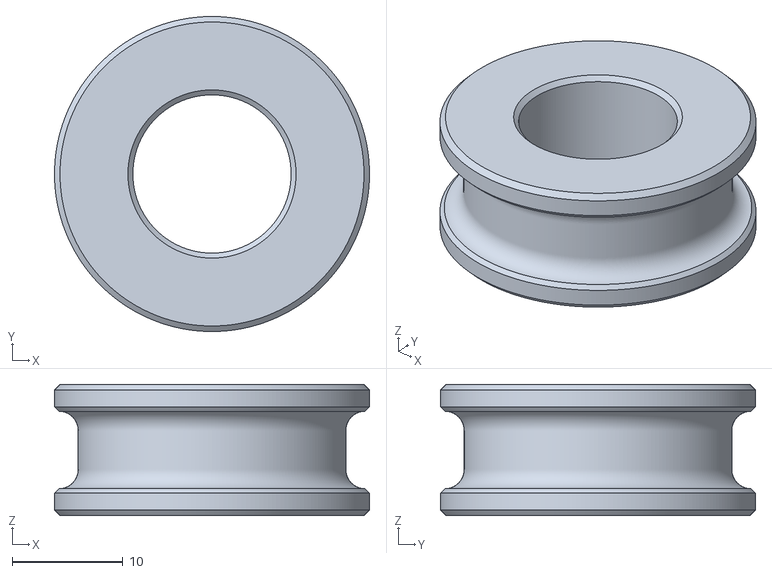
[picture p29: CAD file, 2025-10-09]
Customized Files/Filamentalist V3 Spool Rewinder/Center_Drive_Roller_Assy.stl
28.5 x 28.5 x 11.9

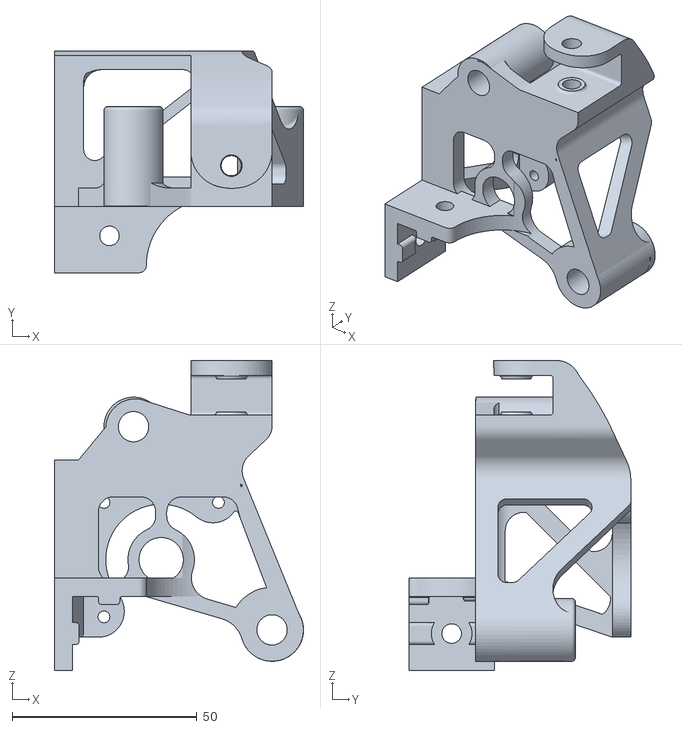
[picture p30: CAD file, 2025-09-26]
Customized Files/Belt Driven/STL/Extruder drive end stronger.stl
67.4 x 60.0 x 83.9

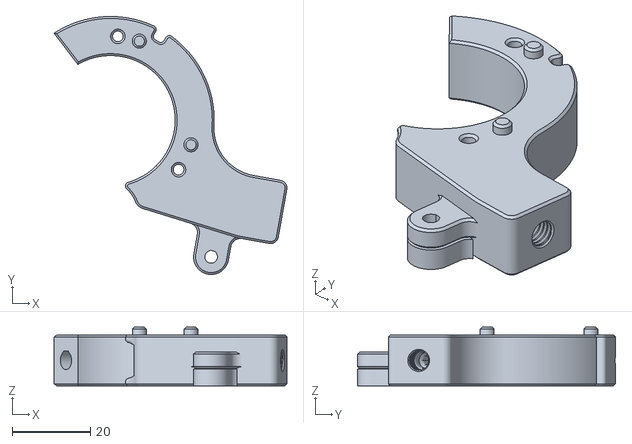
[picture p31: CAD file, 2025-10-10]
Customized Files/Filamentalist V3 Spool Rewinder/Tensioner_Mount_Std_PC4-M6 v4.stl
59.5 x 65.9 x 15.0

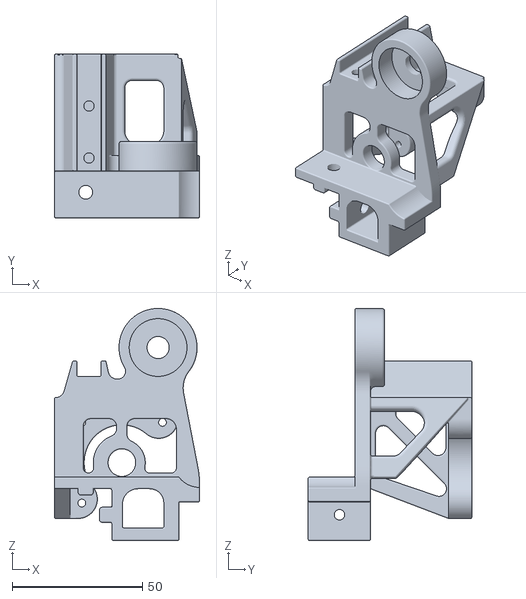
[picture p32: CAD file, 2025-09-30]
Customized Files/Linear Rail/STL/Extruder drive end (Linear).stl
55.9 x 62.9 x 89.2

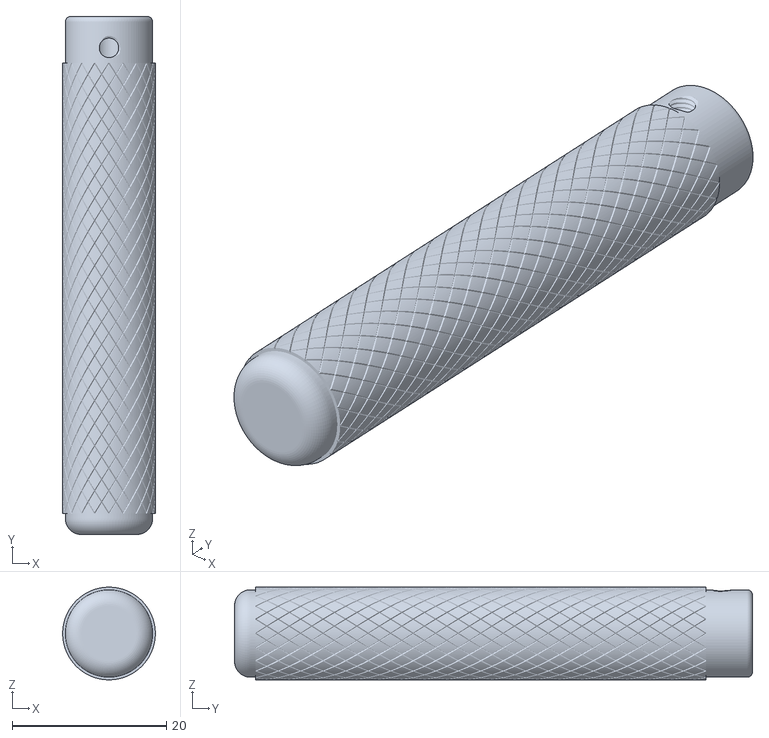
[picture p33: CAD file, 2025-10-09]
Customized Files/M3-Handle.stl
12.0 x 67.3 x 12.0

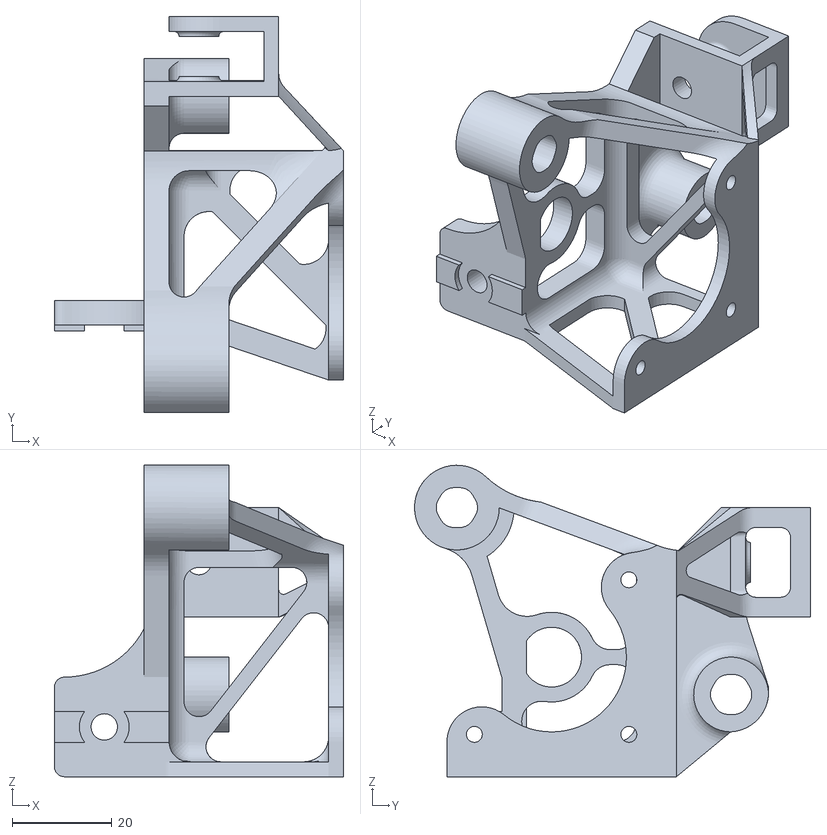
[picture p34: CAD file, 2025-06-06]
V1_Release/CAMMU V1 STL/Extruder drive end.stl
58.0 x 79.4 x 62.5

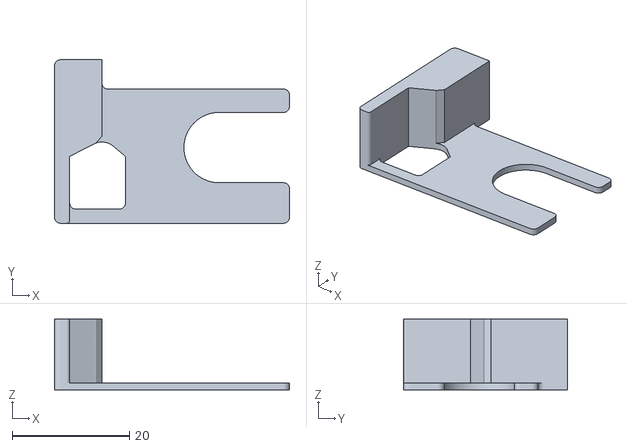
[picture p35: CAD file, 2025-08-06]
V1_Release/CAMMU V1 STL/Gate/CAMMU_Gate_Spacer.stl
40.1 x 27.9 x 12.1

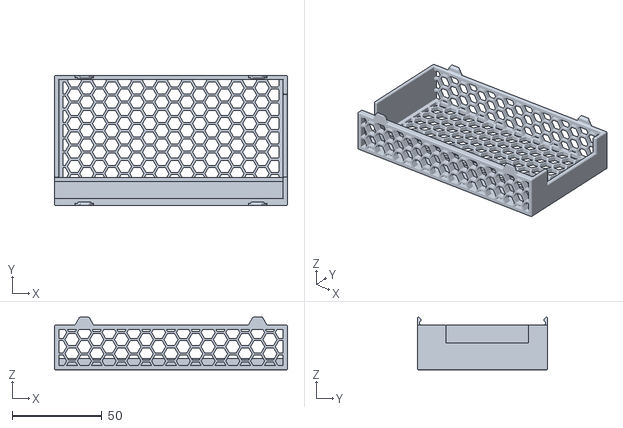
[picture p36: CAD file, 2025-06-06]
V1_Release/Cotton Tail Buffer(ERCT-modified)/Electronic box cover.stl
129.8 x 72.5 x 29.5

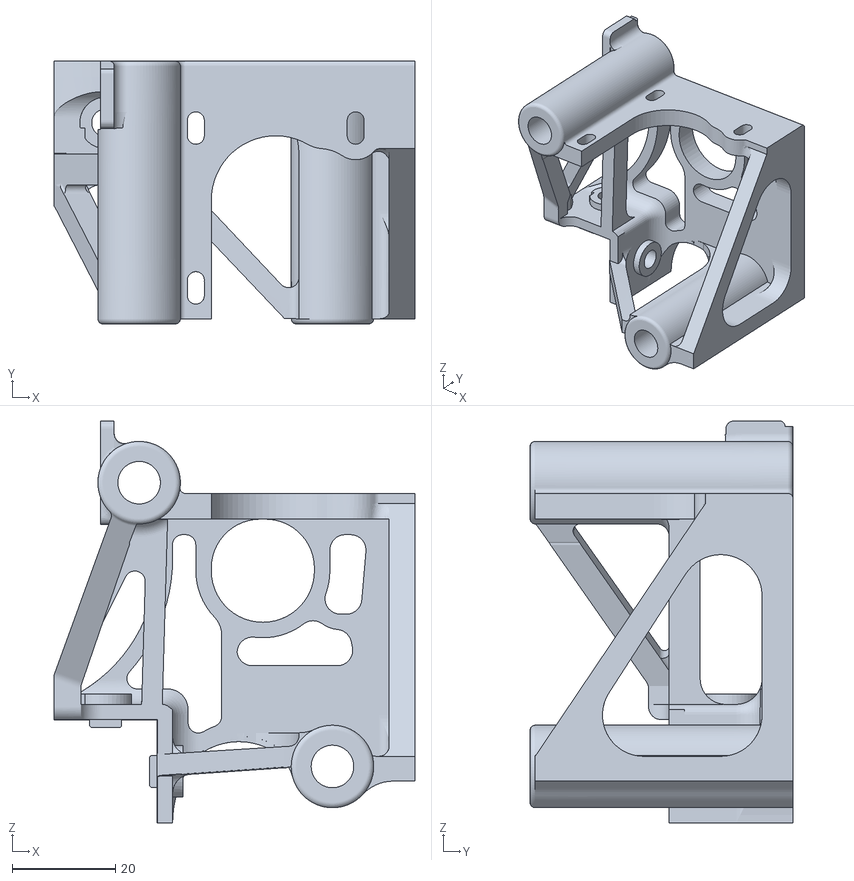
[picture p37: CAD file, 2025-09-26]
Customized Files/Belt Driven/STL/Selector drive end stronger.stl
70.0 x 51.0 x 78.0

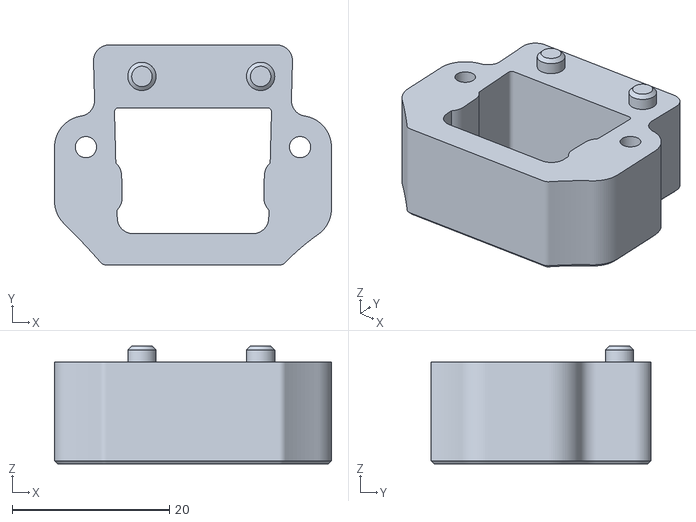
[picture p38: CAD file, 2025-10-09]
Customized Files/Filamentalist V3 Spool Rewinder/Chassis_Cntr_Spacer.stl
35.2 x 28.0 x 15.0

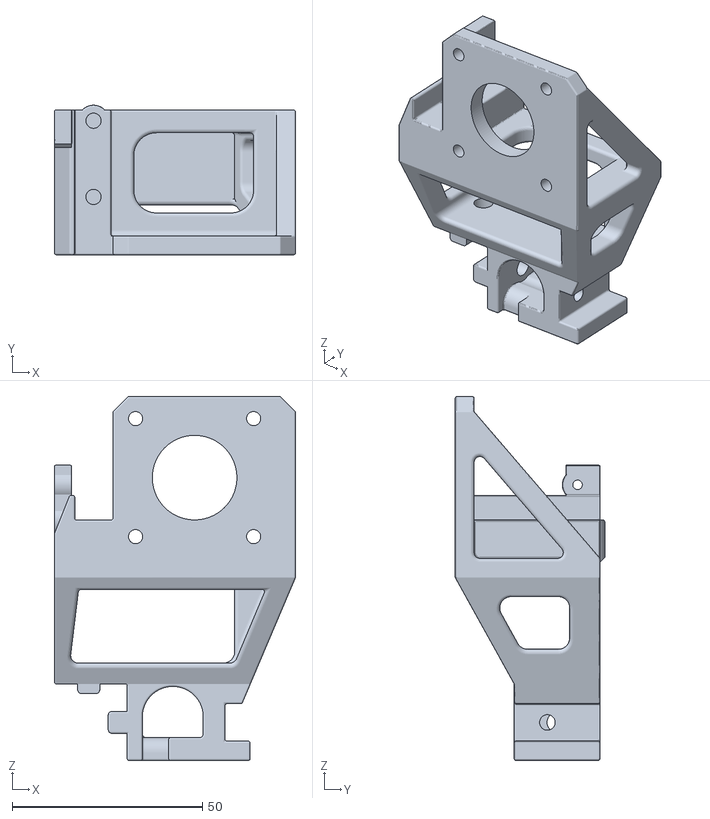
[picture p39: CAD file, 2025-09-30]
Customized Files/Linear Rail/STL/Selector drive end (Coupling).stl
63.3 x 39.3 x 95.6

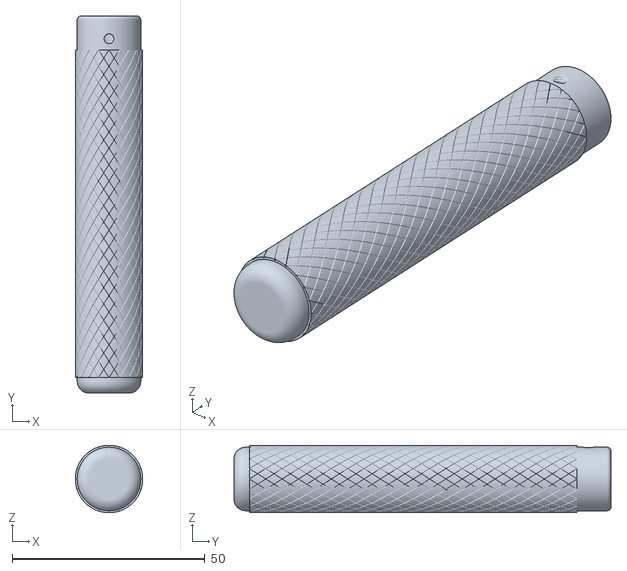
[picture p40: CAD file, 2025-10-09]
Customized Files/M5-Handle.stl
17.5 x 97.8 x 17.5

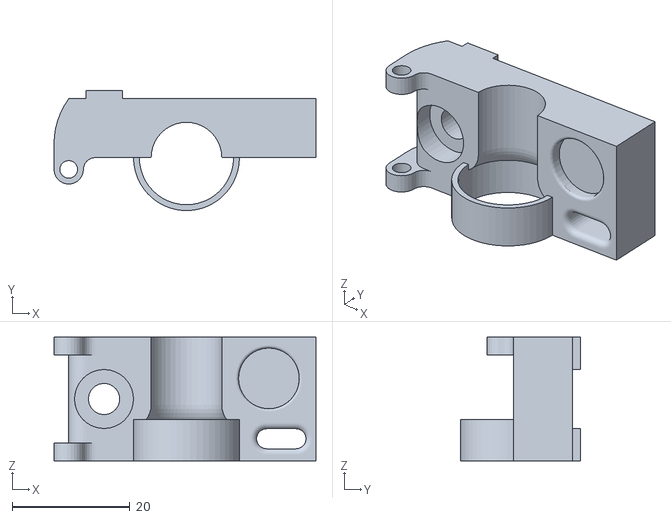
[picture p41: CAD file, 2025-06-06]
V1_Release/CAMMU V1 STL/Gate/Gate bottom.stl
44.5 x 20.4 x 21.0

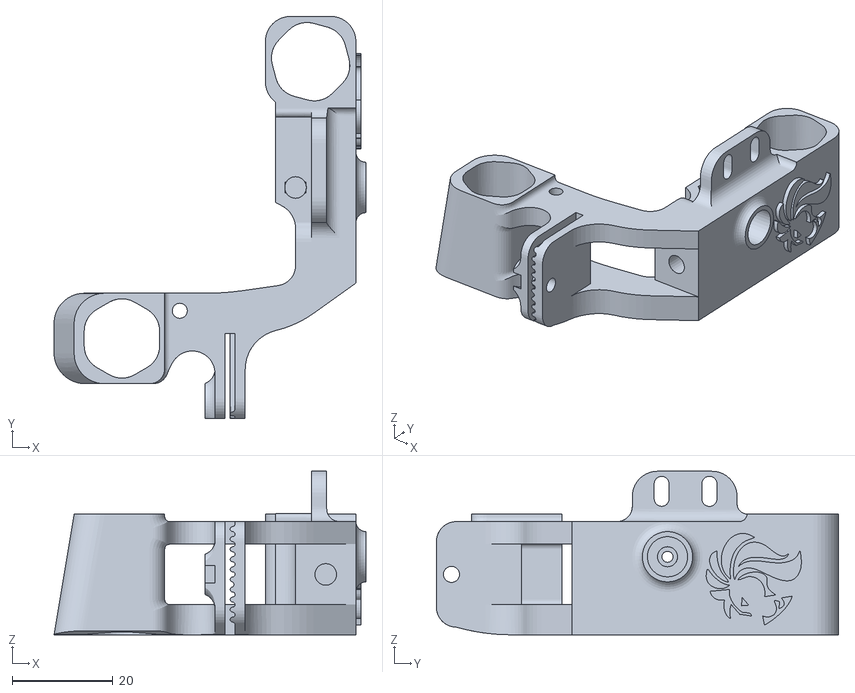
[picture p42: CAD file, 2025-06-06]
V1_Release/CAMMU V1 STL/Selector Body.stl
62.0 x 79.9 x 32.5

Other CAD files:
V1_Release/Cotton Tail Buffer(ERCT-modified)/End cap-No electronics.stl
Customized Files/Belt Driven/STL/Selector Body GT2 Plate Clamp.stl
Customized Files/Filamentalist V3 Spool Rewinder/Fil_Encl_Rear_Mnt_R_608_Bearing_[2020].stl
Customized Files/Linear Rail/STL/Selector Body Linear Rail.stl
CAMMU_Old/CAMMU_Beta_V1/Beta V1 STL/Coupler.stl
CAMMU_Old/CAMMU_Beta_V1/Beta V1 STL/Extruder drive end.stl
CAMMU_Old/CAMMU_Beta_V1/Beta V1 STL/Gate/Gate bottom.stl
CAMMU_Old/CAMMU_Beta_V1/Beta V1 STL/Gate/Gate top.stl
CAMMU_Old/CAMMU_Beta_V1/Beta V1 STL/Selector Body.stl
CAMMU_Old/CAMMU_Beta_V1/Beta V1 STL/Selector drive end.stl
CAMMU_Old/CAMMU_Beta_V1/Beta V1 STL/Tension arm.stl
Customized Files/Belt Driven/STL/Extruder drive end-2020-end-cap (NEW).stl
Customized Files/Belt Driven/STL/Selector drive end-2020-cap (NEW).stl
Customized Files/CAMMU-Gate NEW.step
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

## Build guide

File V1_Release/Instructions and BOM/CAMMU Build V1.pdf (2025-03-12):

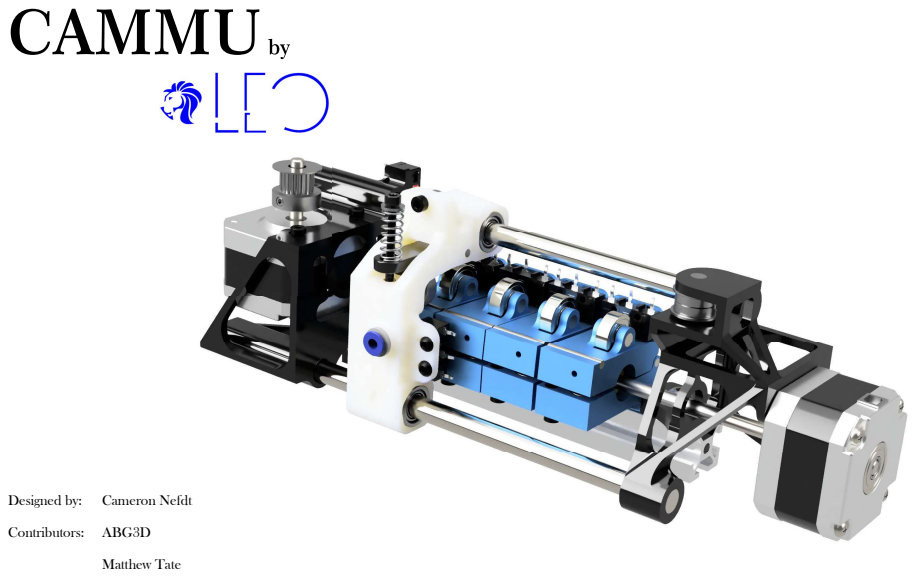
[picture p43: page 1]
Designed by:; Cameron Nefdt; Contributors: ABG3D; Matthew Tate

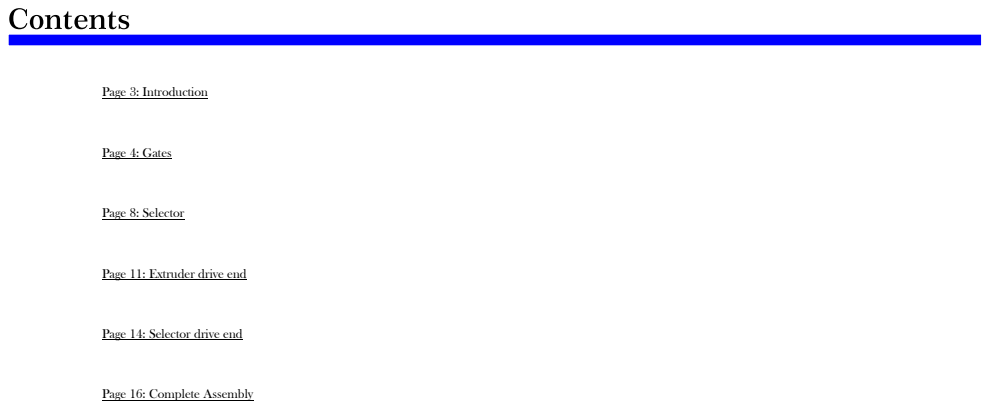
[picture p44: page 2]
Page 3: Introduction; Page 4: Gates; Page 8: Selector

Page 11: Extruder drive end

Page 14: Selector drive end

Page 16: Complete Assembly

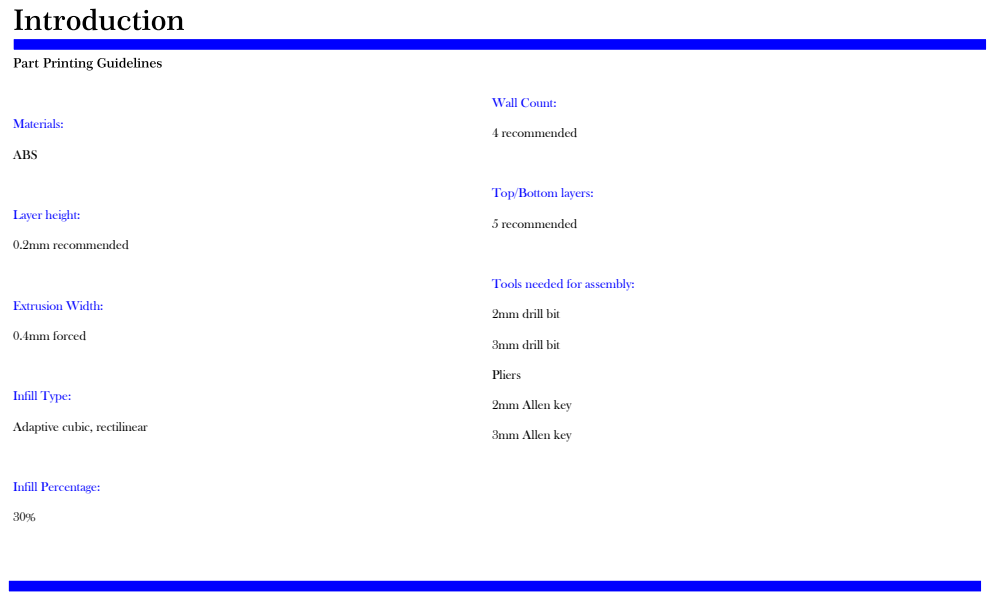
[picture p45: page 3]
Materials:; ABS; Layer height:; 0.2mm recommended; Extrusion Width:; 0.4mm forced; Infill Type:; Infill Percentage:; Wall Count:; 4 recommended; 5 recommended; 2mm drill bit; 3mm drill bit; Pliers; 2mm Allen key; 3mm Allen key

Top/Bottom layers:

Tools needed for assembly:

Adaptive cubic, rectilinear

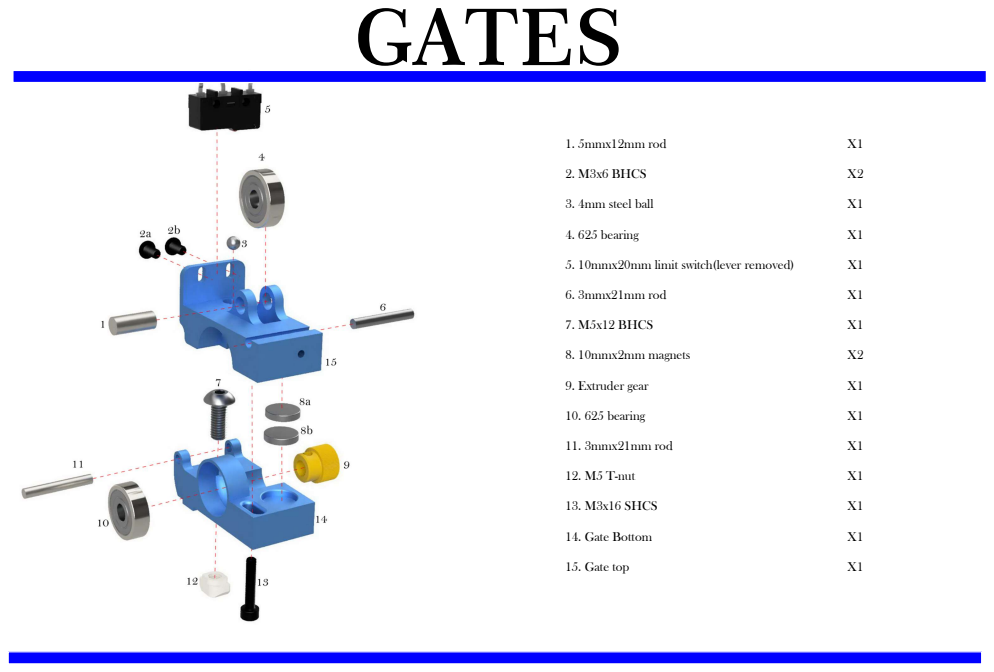
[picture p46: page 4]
1. 5mmx12mm rod; 2. M3x6 BHCS; 3. 4mm steel ball; 4. 625 bearing; 5. 10mmx20mm limit switch(lever removed); 6. 3mmx21mm rod; 7. M5x12 BHCS; 8. 10mmx2mm magnets; 9. Extruder gear; 10. 625 bearing; 11. 3mmx21mm rod; 12. M5 T-nut; 13. M3x16 SHCS; 14. Gate Bottom; 15. Gate top

Using a 3mm drill bit by hand, ream the 2 ears on the bottom gate. Be careful not to go too far and use the 3mm rod to test the fit. The 3mm rod needs to fit tight enough to not move.

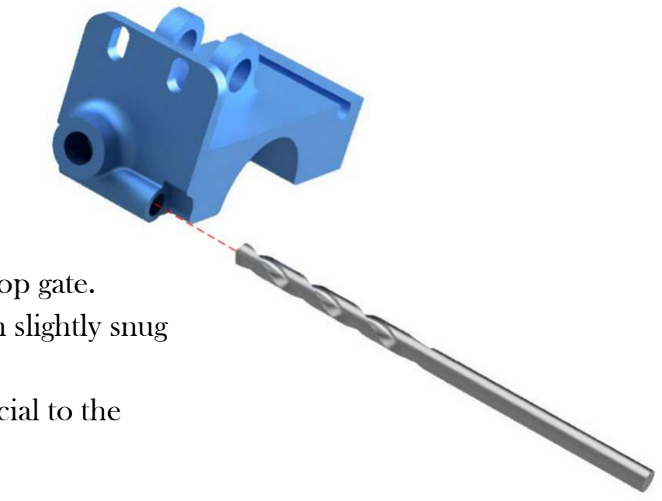
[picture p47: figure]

Using a 3mm drill bit by hand, ream the pivot of the top gate. Using the 3mm rod to test the fit, this needs to slide in slightly snug but not loose.
Be gentle and go slow with this step, the fitment is crucial to the

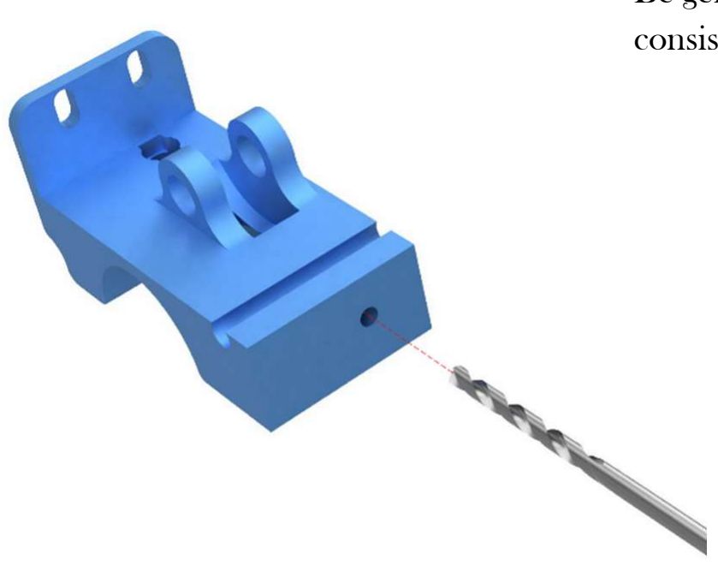
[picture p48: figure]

consistent clamping of the gates.

Use a 2mm drill bit to clean out the filament path on the top gate. You are not trying to widen the hole at all, only ensure that the path is clear.

Fit 1 of the 625 bearings into the bottom gate. Press this in against a hard surface to ensure it goes in even and flat. This will be the drive shaft support.

Fit the M5x12 BCHS through the rear of the bottom gate and attach the M5 T-nut.

Press 1 of the 21mm long 3mm shafts into the rear pivot of the gate. Place one side of the gate against a hard surface while pressing it in.

Place a 625 bearing in the top of the top gate and fit the 12mm long 5mm shaft.

Press a 21mm long 3mm shaft into the top of the gate, ensuring that each end is inline with the sides of the gate.

Insert a 4mm ball bearing into the top of the gate followed by 1 of the limit switches and tighten using 2 of the M3x6mm BHCS. The screws will start grabbing into the limit switch housing and cut its own thread. Use a piece of 1.75mm filament and test the fitment of the limit switch ensuring it enters smooth but consistently triggers the switch.

Press the 2 magnets into place ensuring they are placed as opposing force to one another. These will act as the spring for the gate ensuring it opens and doesn’t grind the filament during use.

Temporarily fit the M3x16 SHCS through the bottom gate and into the top gate. Take care when fitting as to not strip out the threads, this will thread directly into the plastic and acts as a limiter for gate opening movement. It will need to be removed again later when assembling gates onto the extrusion.

Repeat these steps for as many gates as you will be building for

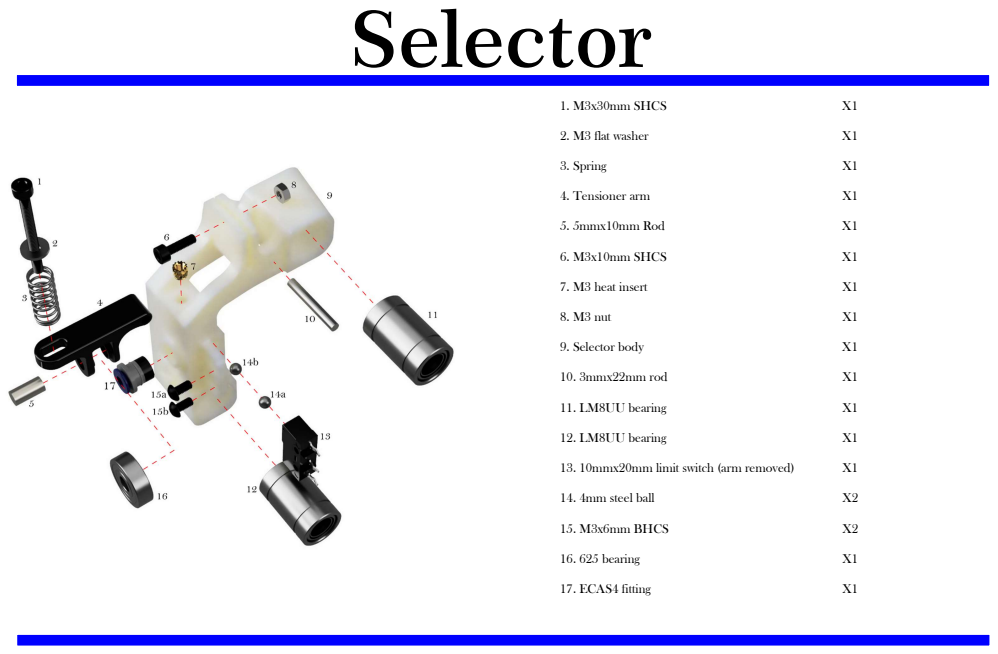
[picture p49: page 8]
1. M3x30mm SHCS; 2. M3 flat washer; 3. Spring; 4. Tensioner arm; 5. 5mmx10mm Rod; 6. M3x10mm SHCS; 7. M3 heat insert; 8. M3 nut; 9. Selector body; 10. 3mmx22mm rod; 11. LM8UU bearing; 12. LM8UU bearing; 13. 10mmx20mm limit switch (arm removed); 14. 4mm steel ball; 15. M3x6mm BHCS; 16. 625 bearing; 17. ECAS4 fitting

Insert the M3 heat insert into the top of the selector body.

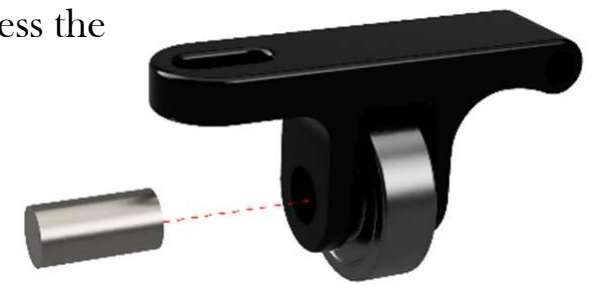
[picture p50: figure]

Fit a 625 bearing in the selector arm and press the 10mm long 5mm shaft in place.

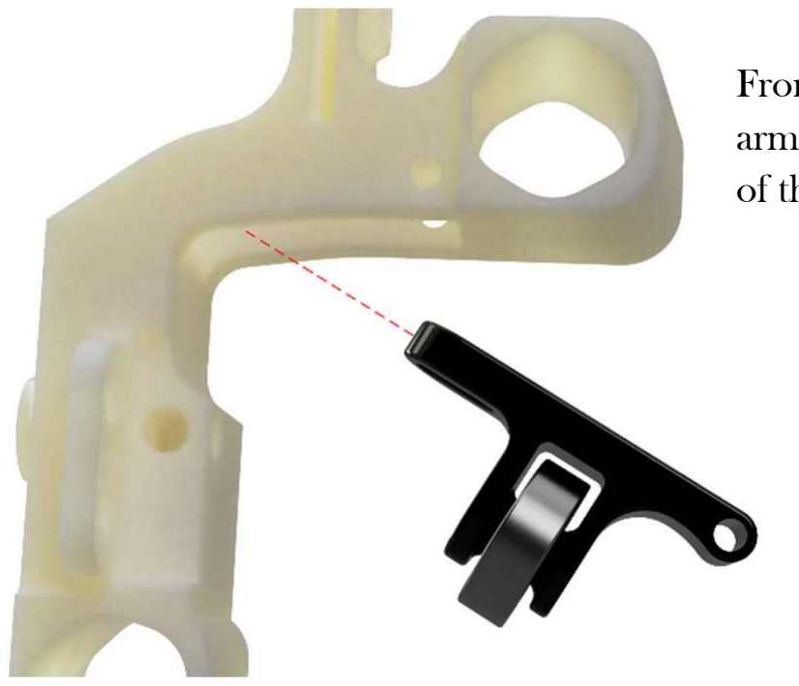
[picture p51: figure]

From behind the selector body, tilt the tension arm at an angle and slide it up and into position of the selector body.

Once the selector arm is in position, you can press the 22mm long 3mm shaft through the selector body and tension arm pivot point. Ensure the tension arm can pivot freely, it only needs a few mm of movement. If the arm pivots too tight, remove it and clear it using a 3mm drill bit.

Press in the 2 LM8UU bearings
into the selector body. | Remove the black rubber piece on the end of
| the ECAS fitting then press the ECAS04 into
| the front of the selector body.

Place 2x 4mm steel balls into the selector body followed by the limit switch. Use 2x M3x6mm screws to tighten into the limit switch. As with the gates, the screws will bite into the limit switch and cut their own threads.

Insert the m3x30mm with the m3 washer and extruder spring through the tension arm and into the heat insert. This does not need to be tensioned yet, just give it a couple rotations to stay in place.

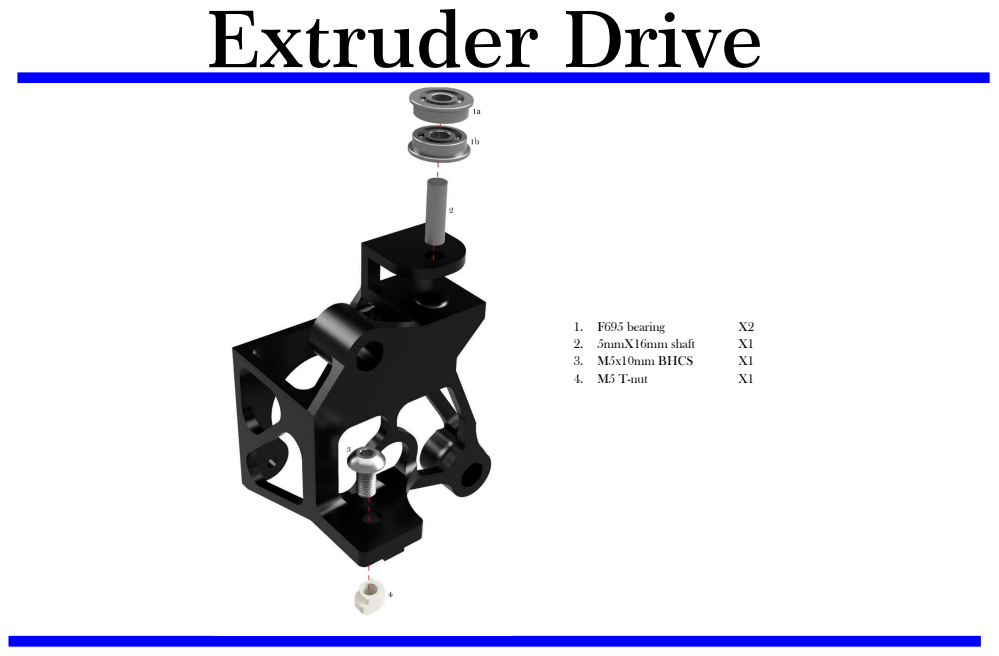
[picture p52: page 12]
1. F695 bearing; 2. 5mmX16mm shaft; 3. M5x10mm BHCS; 4. M5 T-nut

Fit the 2 F695 flanged bearings in the top of the extruder drive end and press in the 5mmX16mm shaft.

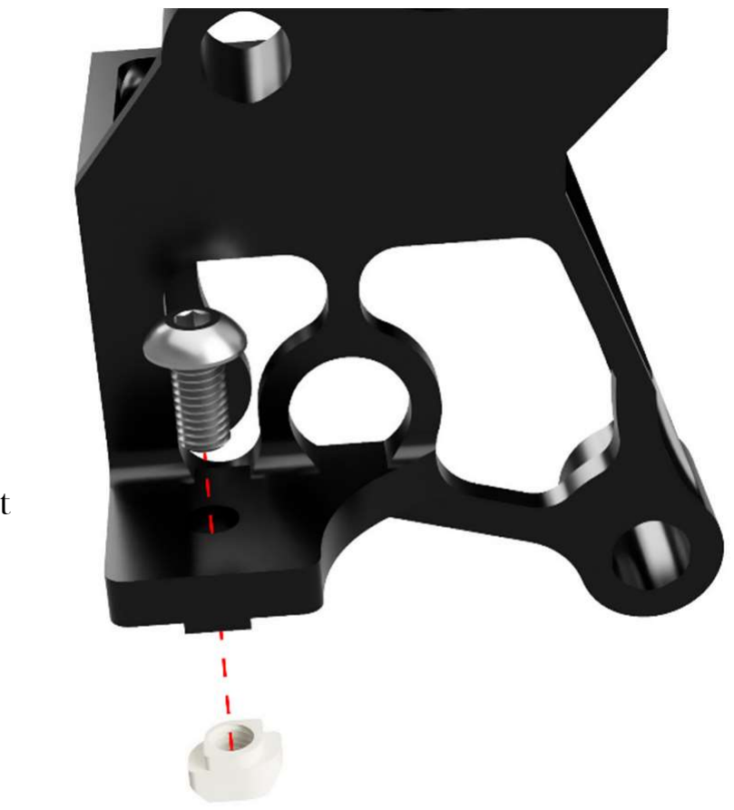
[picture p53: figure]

Fit the m5X10mm screw and M5 T-nut

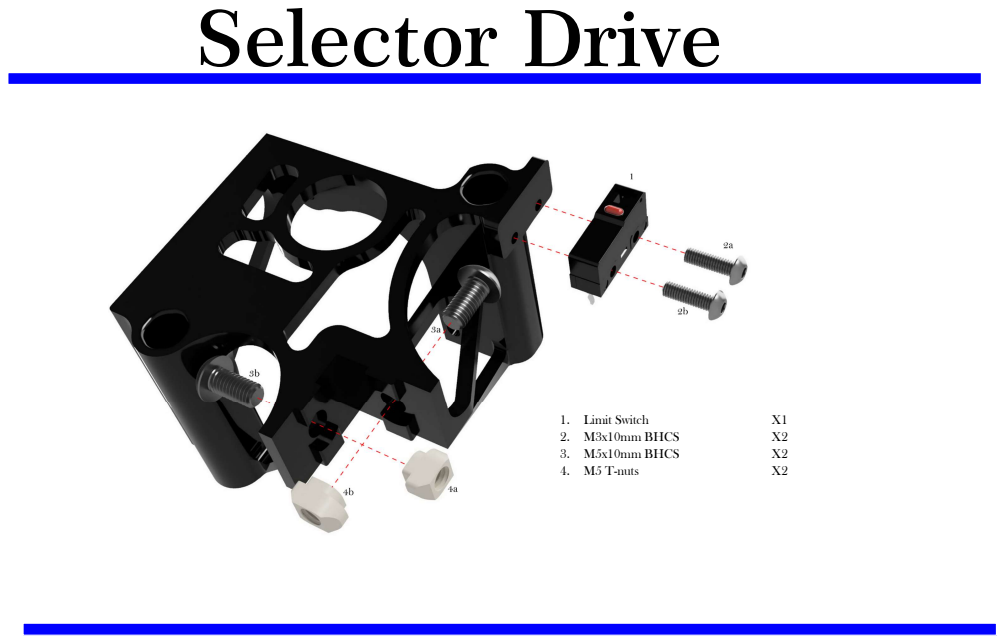
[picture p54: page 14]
1. Limit Switch; 2. M3x10mm BHCS; 3. M5x10mm BHCS; 4. M5 T-nuts

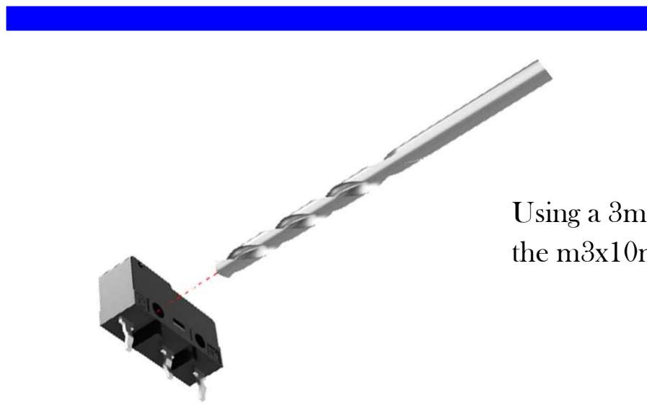
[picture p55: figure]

Using a 3mm drill, make the holes in the limit switch bigger so that the m3x10mm screws can pass through.

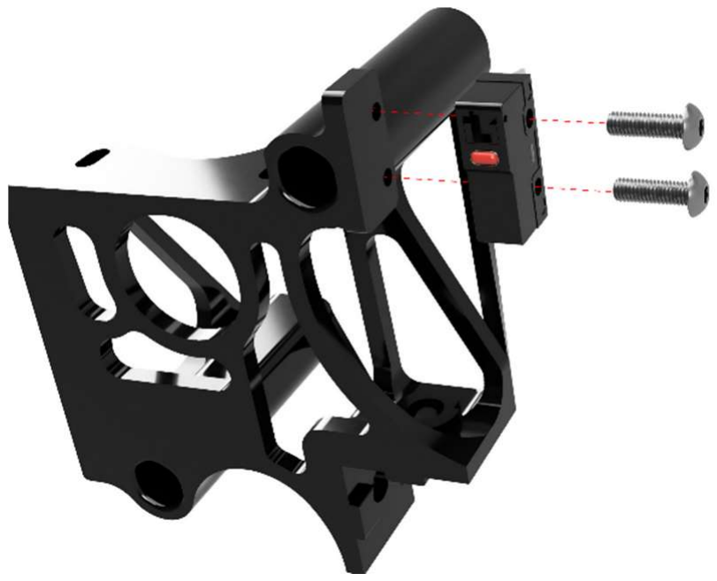
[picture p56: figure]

Fit the limit switch to the side of the selector drive body using the 2 M3x10mm screws.

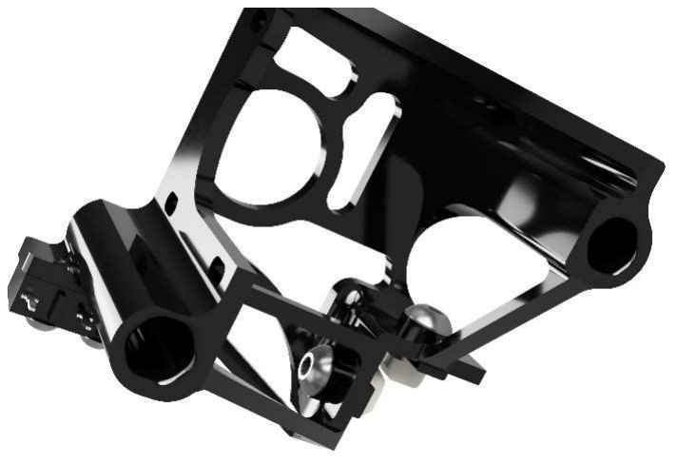
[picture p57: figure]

Fit the 2 M5 T-nuts with the 2 M5x10mm BHCS.

Fit the extruder end frame to the extrusion ensuring the end of the extrusions aligns to the where the angle of the frame bracing starts. The M5 screw can be tightened.

Remove the bottom M3X16mm screw from the bottom of each of the gates. Open them and fit each gate to the extrusion starting with the one closest to the extruder frame, placing it 2-3mm from the frame attachment to the extrusion. Then fit the rest of the gates placing them approximately 1mm apart from one another ensuring the gaps are even and the gates are straight with one another. Leave the M3x16mm screws out for now until the extruder gears and drive shafts in place.

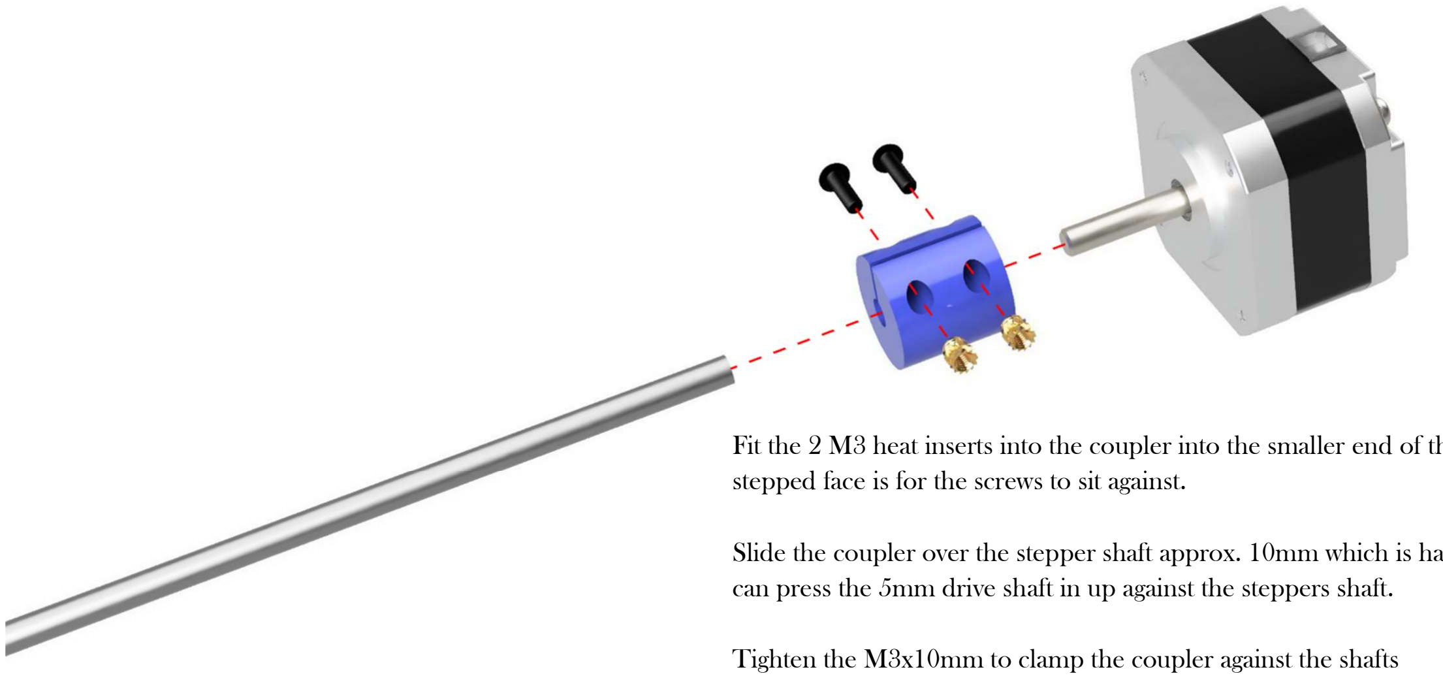
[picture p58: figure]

Fit the 2 M3 heat inserts into the coupler into the smaller end of the through holes. The side with the stepped face is for the screws to sit against.

Slide the coupler over the stepper shaft approx. 10mm which is half way in the coupler. Then you can press the 5mm drive shaft in up against the steppers shaft.

Tighten the M3x10mm to clamp the coupler against the shafts

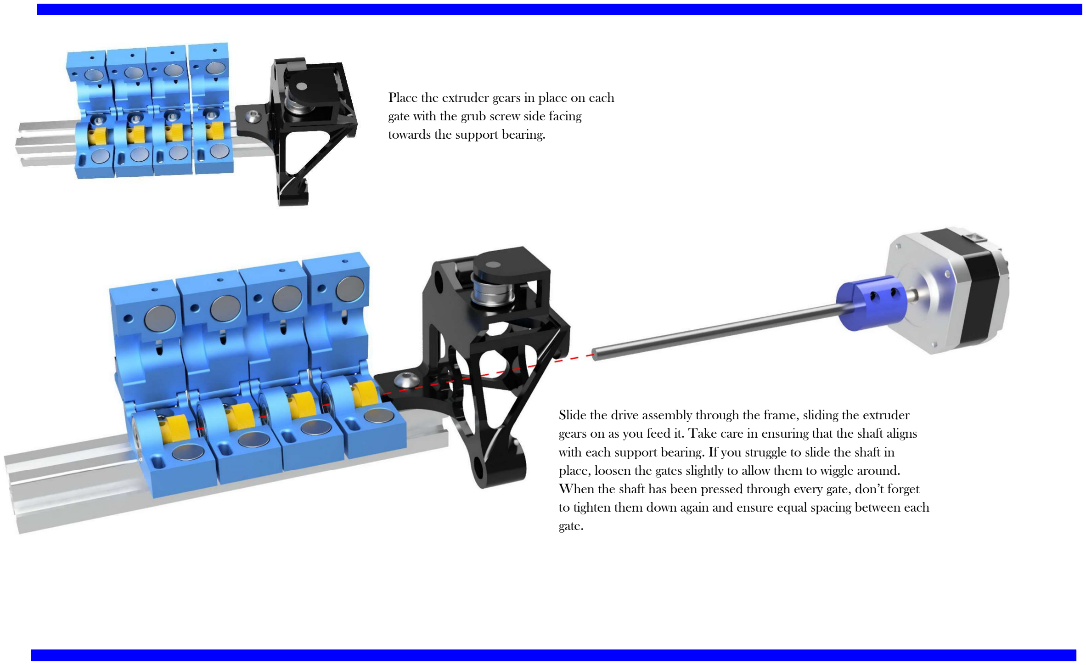
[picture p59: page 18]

Place the extruder gears in place on each gate with the grub screw side facing towards the support bearing.

Slide the drive assembly through the frame, sliding the extruder gears on as you feed it. Take care in ensuring that the shaft aligns with each support bearing. If you struggle to slide the shaft in place, loosen the gates slightly to allow them to wiggle around. When the shaft has been pressed through every gate, don’t forget to tighten them down again and ensure equal spacing between each gate.

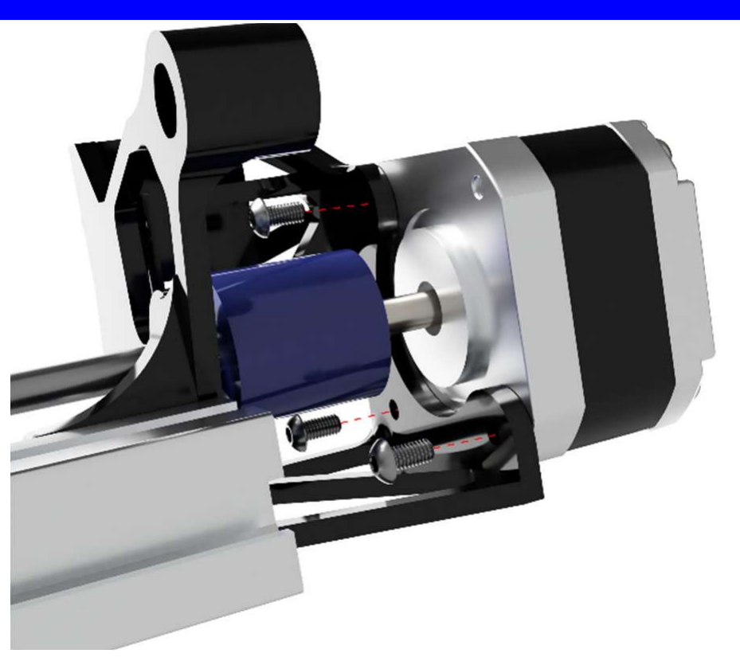
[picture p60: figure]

With the stepper now in place against the extruder drive end frame, use 3 M3x6mm BHCS to tighten the extruder in place

Aligning the centre of the extruder gear teeth with the centre of the filament path, you can now tighten the extruder gears in place

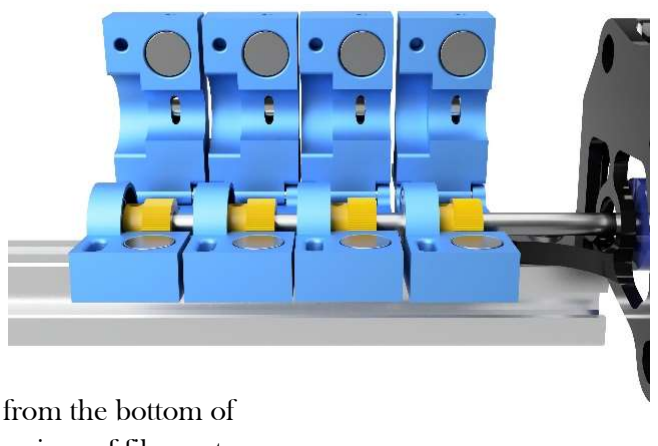
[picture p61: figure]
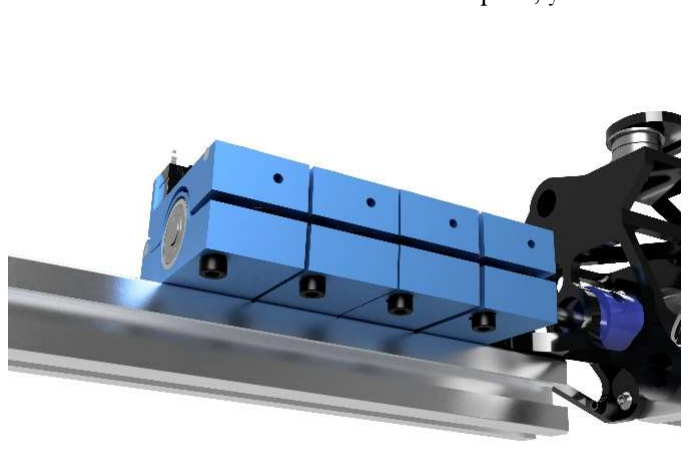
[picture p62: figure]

The stopper screws can now be placed back in from the bottom of the gates and each individually adjusted. Using a piece of filament, place it through the filament pathway in the top gate. Tighten the bottom adjuster until you can just start to feel the extruder gear grabbing the filament, then back it off 2 full rotations.

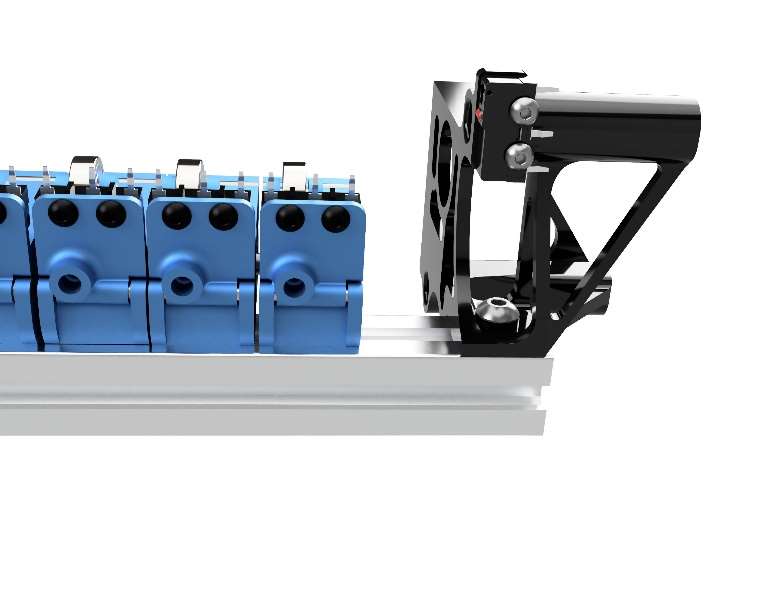
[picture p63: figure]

Slide the selector drive side frame into place on the extrusion positioning it approximately 20mm from the final gate, tighten the mounting screws. This empty space will be the ‘neutral’ position for the selector.

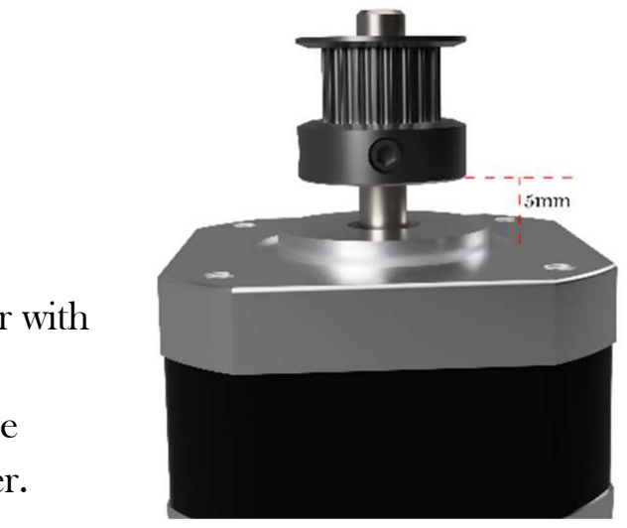
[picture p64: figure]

Fit the 20T pulley to the stepper with the bottom of the pulley
approximately 5mm up from the mounting surface of the extruder.

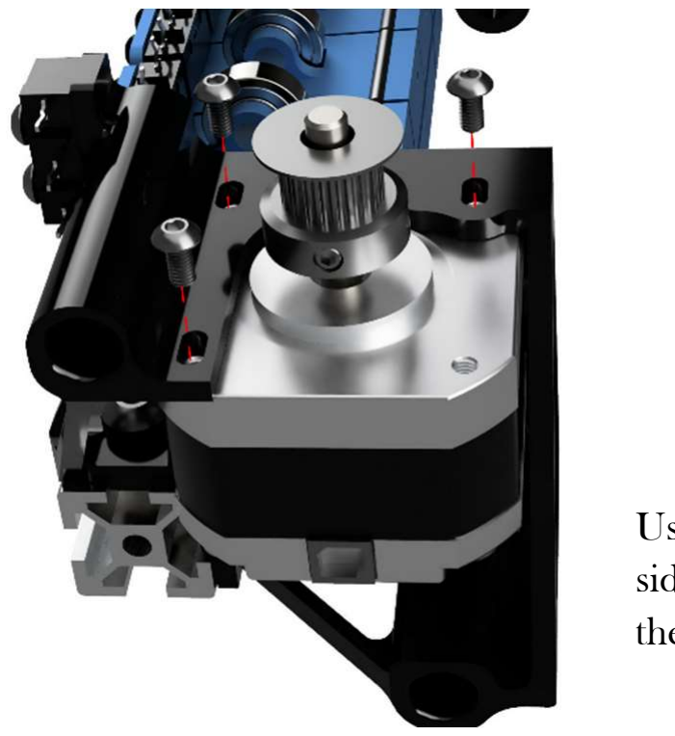
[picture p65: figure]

Using 3 M3x6mm BHCS, mount the servo to the selector drive side frame. Leave these slightly loose as this will be used to tension the selector belt.

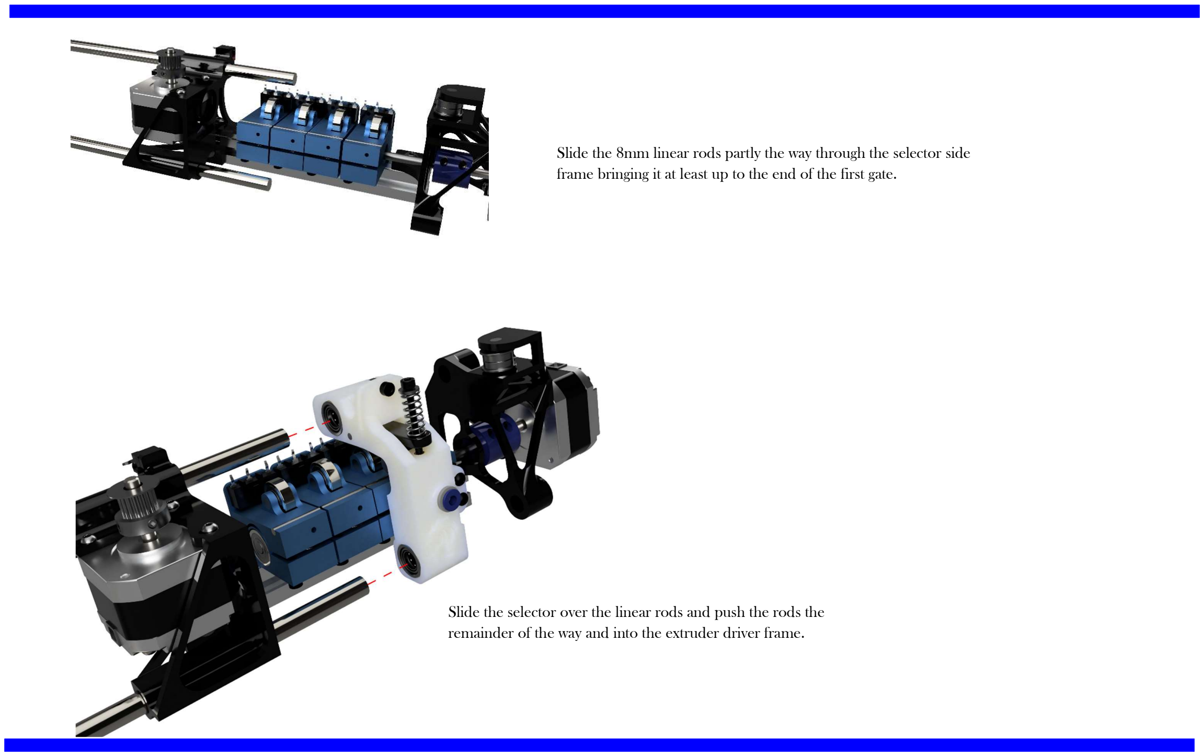
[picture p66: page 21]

Slide the 8mm linear rods partly the way through the selector side frame bringing it at least up to the end of the first gate.

Slide the selector over the linear rods and push the rods the remainder of the way and into the extruder driver frame.

Slide in one side of the belt 3 or 4 teeth in on the top of the selector. Then feed it across and around the pulley on the stepper, across to the other side, around the idler pulley and back across to the selector. Trim the belt so that only 3 or 4 teeth will fit in the selector body while pulling slight tension on the belt. Fit the M3X10mm screw and m3 nut to hold the belt in place. This does not need to be very tight as this only helps to keep the belt clamped but doesn’t clamp the belt itself.

You can now tighten the screws for the selector side stepper while pulling the stepper out slightly to add a little more tension on the belt. The belt does not need a lot of tension so only slight pressure is required.

Assembly of your CAMMU is now complete and all that is left is wiring, setup and fine tuning. We have not included a wiring guide at this point because the wiring layout and choices depends on the decision of controller and this will be covered in a separate guide.

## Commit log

2024-11-01 CAMMU V1-Beta STL
    [BOM.xlsx, Coupler.stl, Extruder drive end.stl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]
2024-11-04 Orientation changed
    Oriented correctly for printing
    [Gate bottom.stl]
2024-11-04 Orientation changed
    Oriented files correctly for printing
    [Extruder drive end.stl, Selector Body.stl]
2024-11-06 Corrected BOM
    [BOM.xlsx]
2024-11-08 Add files via upload
    Replacement bottom gate with bearing tollerance
    [Gate bottom.stl]
2024-11-08 Orientation Updated
    Chaned printing orientation
    [Gate bottom.stl]
2024-11-08 Add files via upload
    Tension arm size update
    [Tension arm.stl]
2024-11-08 Printing Orientation Update
    Updated orientation for printing
    [Tension arm.stl]
2024-11-08 Updated BOM
    Updated the BOM with links and quantities
    [BOM.xlsx]
2024-11-08 Updated BOM
    Added the MCU to the BOM
    [BOM.xlsx]
2024-11-09 Add files via upload
    Updated top gate with 3mm slot to hold rod better
    [Gate top.stl]
2025-06-06 V1 Release
    Full V1 Release
    [BOM.xlsx, Buffer body W bunny.stl, Buffer body-No bunny.stl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]
2025-06-06 Updated folder structure
    [BOM.xlsx, Buffer body W bunny.stl, Buffer body-No bunny.stl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]
2025-06-06 Edit Readme.md
    [Coupler.stl, Extruder drive end.stl, Gate bottom.stl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]
2025-06-06 Tidy up folders and files
    [BOM.xlsx, Buffer body W bunny.stl, Buffer body-No bunny.stl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]
2025-06-06 Uploaded images
    [BOM.xlsx, Buffer body W bunny.stl, Buffer body-No bunny.stl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]
2025-06-06 Updated gate bottom orientation
    [Gate bottom.stl]
2025-06-06 stl orientation updated
    [Buffer body W bunny.stl, Buffer body-No bunny.stl, Electronic box cover.stl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]
2025-08-06 Added Gate Spacer
    [CAMMU_Gate_Spacer.stl]
2025-09-25 add Customized Files
    Stronger gate files
    [Gate bottom (NEW).stl, Gate top (NEW).stl]
2025-09-25 Update Gate top (NEW).stl
    [Gate top (NEW).stl]
2025-09-26 updated files
    [Extruder drive end (Linear).stl, Extruder drive end-2020-end-cap (NEW).stl, Extruder drive end-2020-end-cap.stl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]
2025-09-26 updated step and files
    [Extruder drive end stronger.stl, Extruder drive end-Stronger.stl, Selector drive end stronger.stl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]
2025-09-27 new thicker Gate top
    [Gate top (NEW) (Thicker).stl]
2025-09-27 updated parts
    [CAMMU-Gate v9.step, Gate bottom (NEW).stl, Gate top (NEW) (Thicker).stl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]
2025-09-28 updated the gate files
    [CAMMU-Gate v9.step, CAMMU-Gate.step, Gate bottom (NEW).stl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]
2025-09-28 made tolerance adjustment on NEW gate parts
    [CAMMU-Gate.step, Gate top (NEW).stl]
2025-09-28 flipped gate stl files on printable sides
    [Gate bottom (NEW).stl, Gate top (NEW).stl]
2025-09-29 added Slider-Nut-Spacer-12mm
    updated cad file and added added Slider-Nut-Spacer-12mm stl file
    [CAMMU-Gate NEW.step, CAMMU-Gate.step, Slider-Nut-Spacer-12mm.stl]
2025-09-30 fixed extruder end mount for long shaft steppers
    [Extruder drive end (Linear).stl, Selector drive end (Coupling).stl]
2025-10-09 added Filamentalist - Spool Rewinder
    My customized Filamentalist - Spool Rewinder parts and tools
    [Center_Drive_Roller_Assy.stl, Chassis_Cntr_Spacer.stl, Chassis_L_608_Bearing(Mirror).stl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]
2025-10-09 added cad files
    added some cad files
2025-10-09 added test video and code
    Test CAMMU with Arduino-ramps
2025-10-09 added PC4-M6 Gate file
    [Gate top (NEW)-PC4-M6.stl]
2025-10-09 Drill Bit Handle v2
    [M3-Handle.stl, M4-Handle.stl, M5-Handle.stl]
